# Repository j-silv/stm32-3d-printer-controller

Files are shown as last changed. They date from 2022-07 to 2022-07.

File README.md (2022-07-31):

# STM32 Nucleo 3D printer controller
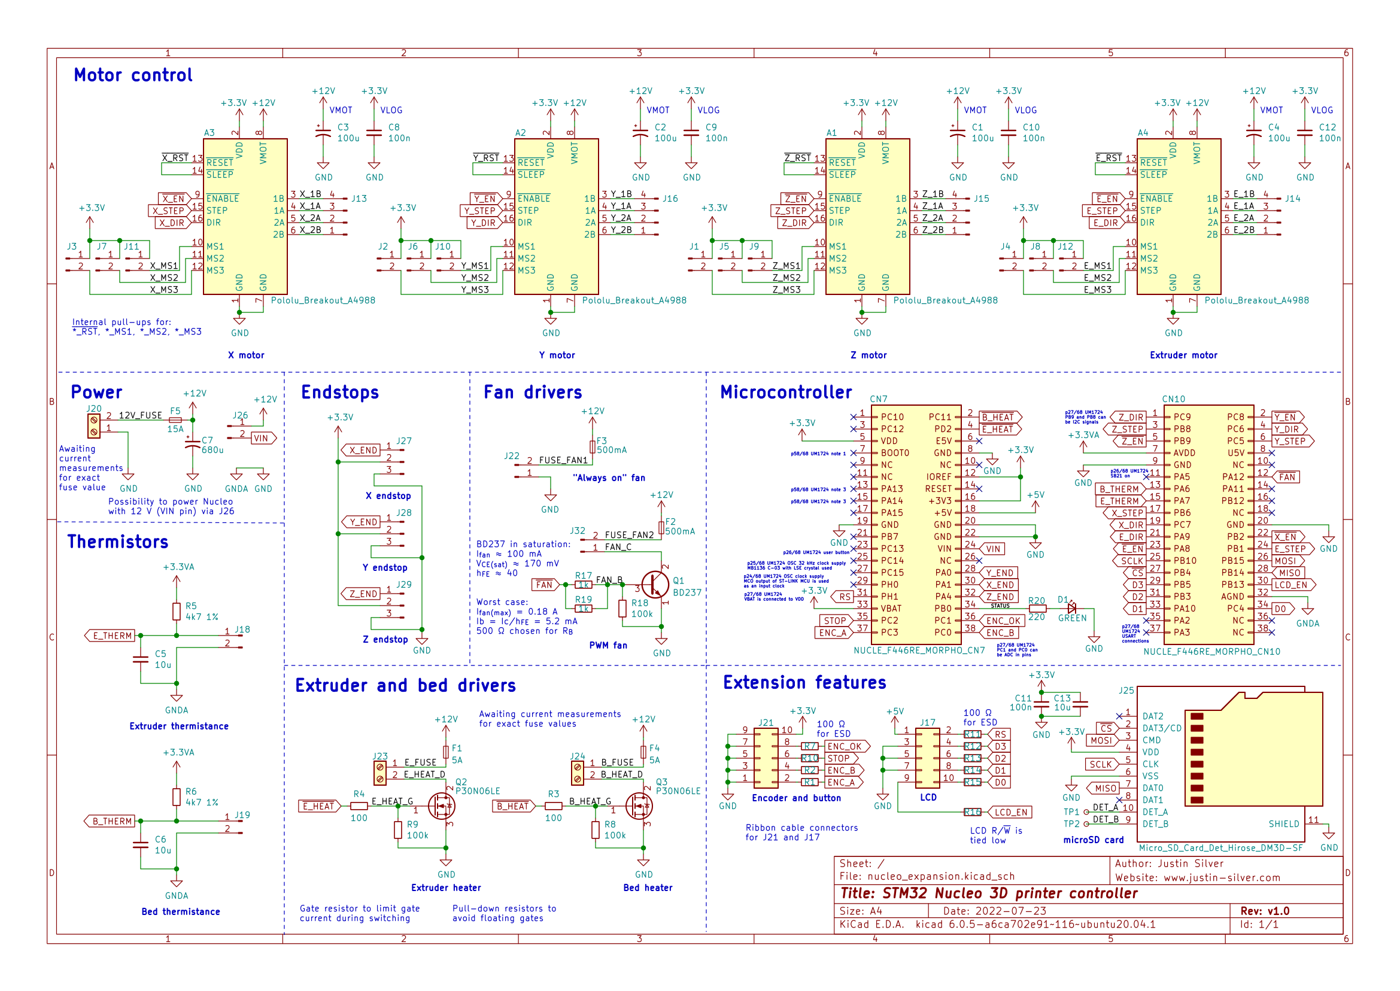
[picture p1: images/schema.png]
Kicad schematic

This project concerns the replacement of a Teensylu 3D printer controller board for a [uDelta RepRap printer](https://reprap.org/wiki/Micro_Delta). An STM32 NUCLEO-F446RE expansion board (shield) is currently being developed as the replacement. After the board is designed and fabricated, the Marlin open source firmware will be configured for use with the Nucleo board.

# Folder structure

**./kicad/stm32_nucleo_expansion/**
- Contains all the CAD files for the shield PCB

# Power usage
I will be using a [S-240-12 12 V 240 W power supply](https://www.meanwellusa.com/upload/pdf/SP-240/SP-240-spec.pdf) Here is an approximate distribution of the power consumption:

## High power usage

### Pololu stepper motors
- [StepStick from RepRap](https://www.reprap-france.com/produit/363-pilote-de-moteur-pas-a-pas-stepstick)
- Max current of 2 A per coil, with overcurrent output protection at 2.1 A
- On-board current limit via potentiometer needs to be checked (TODO)

### Extruder
- 12 V, 3.5 A (40 W) [as specified here](https://www.reprap-france.com/produit/380-cartouche-de-chauffe-12v-40w)

### Bed
- 12 V, 3.5 A (40 W) [as specified here](https://www.reprap-france.com/produit/1234568345-kit-plateau-chauffant-pour-microdelta-originale)

### Extruder fans
- 12 V, 0.18 A (2.16 W) [as specified here](https://www.reprap-france.com/produit/1234568367-ventilateur-turbine-40x10mm-12v)

## Low power usage

### NUCLEO-F446RE
- Supplied with USB 5 V: [300 mA max input current](https://www.st.com/resource/en/user_manual/um1724-stm32-nucleo64-boards-mb1136-stmicroelectronics.pdf#page=20)
- Supplied with external 12 V: [250 mA max input current](https://www.st.com/resource/en/user_manual/um1724-stm32-nucleo64-boards-mb1136-stmicroelectronics.pdf#page=21)
- Measure current consumed by NUCLEO board via JP5 (TODO)

### Pololu stepper motors
- [Approximately 15 mA consumption](https://www.pololu.com/file/0J450/A4988.pdf) at 3.3 V: 50 mW

### microSD card
- [Approximately 150 mA for standard mode (25 MHz) at 3.3 V](https://images-na.ssl-images-amazon.com/images/I/91tTtUMDM3L.pdf): 500 mW

### LCD
- [Typical 1.1 mA consumption](https://www.openhacks.com/uploadsproductos/eone-1602a1.pdf). At 5 V: 5 mW

# PCB
The shield is a 2-layer board fabricated by JLCPCB. It plugs directly into the NUCLEO-F446RE via two 38-pin morpho connectors.
Top and bottom layer view of PCB

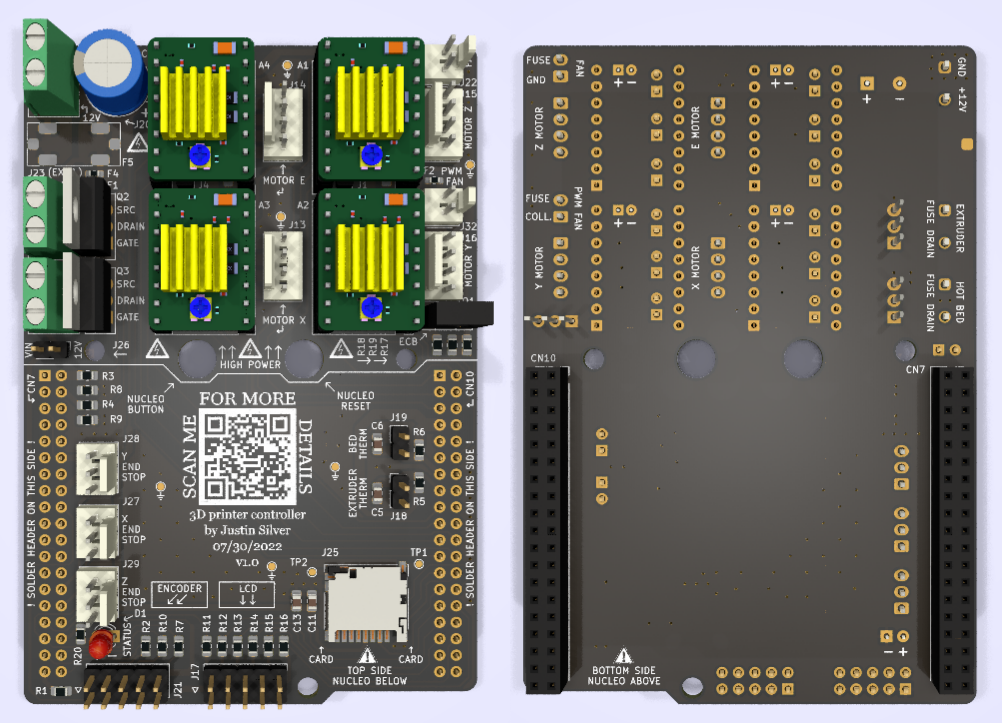
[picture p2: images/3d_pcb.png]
3D view of PCB


# Acknowledgments

- Design inspired by [Teensylu RepRap](https://reprap.org/wiki/Teensylu/fr)
- Kudos to [mobilinkd](https://github.com/mobilinkd/stm-morpho-template) for the STM32 morpho connector template
- Kudos to [bettak](https://grabcad.com/library/reprap-stepstick-stepper-motor-driver-module-1) for the RepRap StepStick 3D model
- Thanks to [r/PrintedCircuitBoard on Reddit](https://www.reddit.com/r/PrintedCircuitBoard/) for the advice and comments

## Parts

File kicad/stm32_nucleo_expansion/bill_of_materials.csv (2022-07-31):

Item | Qty | Reference(s) | Value | DigiKey ID | Product
1 | 4 | A1, A2, A3, A4 | Pololu_Breakout_A4988 |  | STEPPER-DRIVER-STEPSTICKS-A4988
2 | 4 | C1, C2, C3, C4 | 100u | 399-6102-ND | ESK107M025AC3AA
3 | 3 | C5, C6, C13 | 10u | 1276-1096-1-ND | CL21A106KOQNNNE
4 | 1 | C7 | 680u | 732-8638-1-ND | 860010475015
5 | 5 | C8, C9, C10, C11, C12 | 100n | 1276-1003-1-ND | CL21B104KBCNNNC
6 | 1 | CN7 | NUCLE_F446RE_MORPHO_CN7 | S7122-ND | PPPC192LFBN-RC
7 | 1 | CN10 | NUCLE_F446RE_MORPHO_CN10 | S7122-ND | PPPC192LFBN-RC
8 | 1 | D1 | GREEN
9 | 2 | F1, F4 | 5A | 2315-FMC16502WHTPCT-ND | FMC16502WHTP
10 | 2 | F2, F3 | 500mA | 2315-FMC16501WHTPCT-ND | FMC16501WHTP
11 | 1 | F5 | 15A | 36-3586-ND and F11955-ND | 3586 and 0297015.WXT
12 | 15 | J1, J2, J3, J4, J5, J6, J7, J8, J9, J10, J11, J12, J18, J19, J26 | Conn_01x02_Male
13 | 4 | J13, J14, J15, J16 | Conn_01x04_Male | WM19478-ND | 22280040
14 | 2 | J17, J21 | Conn_02x05_Counter_Clockwise
15 | 3 | J20, J23, J24 | Screw_Terminal_01x02 | 732-10955-ND | 691137710002
16 | 2 | J22, J32 | Conn_01x02_Male | WM19485-ND | 22281020
17 | 1 | J25 | Micro_SD_Card_Det_Hirose_DM3D-SF | H126097CT-ND | DM3D-SF(41)
18 | 3 | J27, J28, J29 | Conn_01x03_Male | WM2792-ND | 22280030
19 | 1 | Q1 | BD237 |  | BD237
20 | 2 | Q2, Q3 | P30N06LE |  | P30N06LE
21 | 12 | R1, R2, R3, R4, R7, R10, R11, R12, R13, R14, R15, R16 | 100 | RHM100KCT-ND | ESR10EZPJ101
22 | 2 | R5, R6 | 4k7 1% | A129546CT-ND | CRGH0805F4K7
23 | 3 | R8, R9, R18 | 100k | RHM100KKCT-ND | ESR10EZPJ104
24 | 2 | R17, R19 | 1k | RNCP0805FTD1K00CT-ND | RNCP0805FTD1K00
25 | 1 | R20 | 220
26 | 2 | TP1, TP2 | TestPoint_Small

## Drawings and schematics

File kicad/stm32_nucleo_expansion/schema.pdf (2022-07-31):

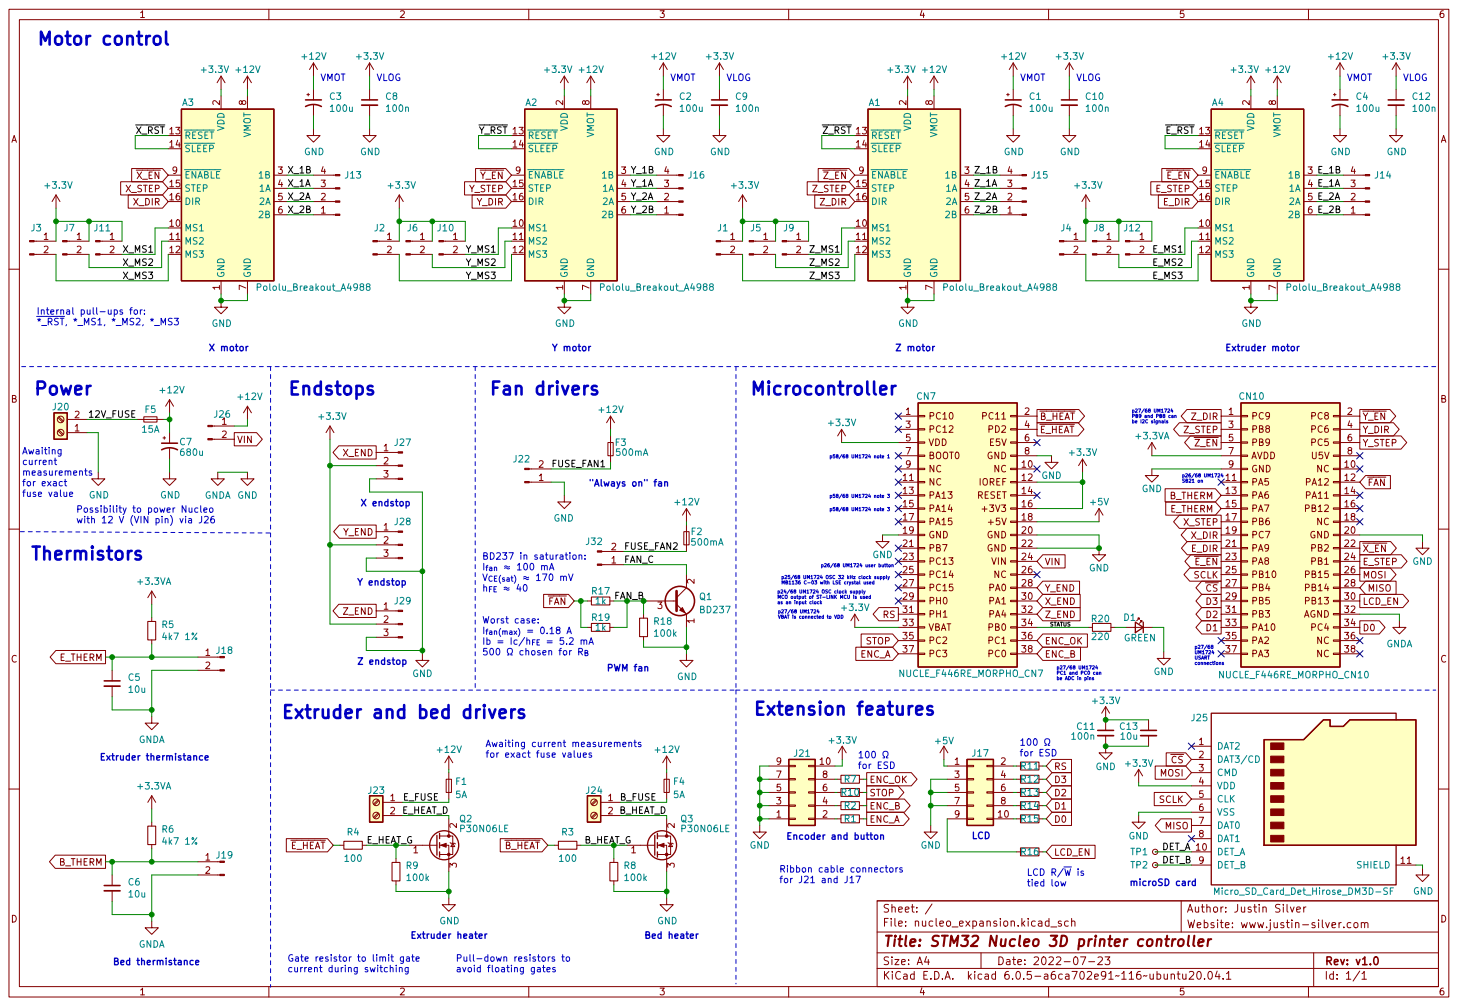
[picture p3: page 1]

p26/68 UM1724 SB21 on Y motor Motor control

1 MS1 10 MS2 11 MS3 12 ~{RESET} 13 ~{SLEEP} 14 STEP 15 DIR 16 VDD

Internal pull-ups for:

Possibility to power Nucleo
with 12 V (VIN pin) via J26
Thermistors

PWM fan BD237 in saturation: þÿI_{fan} "H 100 mA

p25/68 UM1724 OSC 32 kHz clock supply MB1136 C-03 with LSE crystal used

p24/68 UM1724 OSC clock supply MCO output of ST-LINK MCU is used as an input clock p27/68 UM1724 VBAT is connected to VDD

I_{fan(max)} = 0.18 A

be ADC in pins Extruder and bed drivers

for exact fuse values Gate resistor to limit gate

Id: 1/1 Title: STM32 Nucleo 3D printer controller

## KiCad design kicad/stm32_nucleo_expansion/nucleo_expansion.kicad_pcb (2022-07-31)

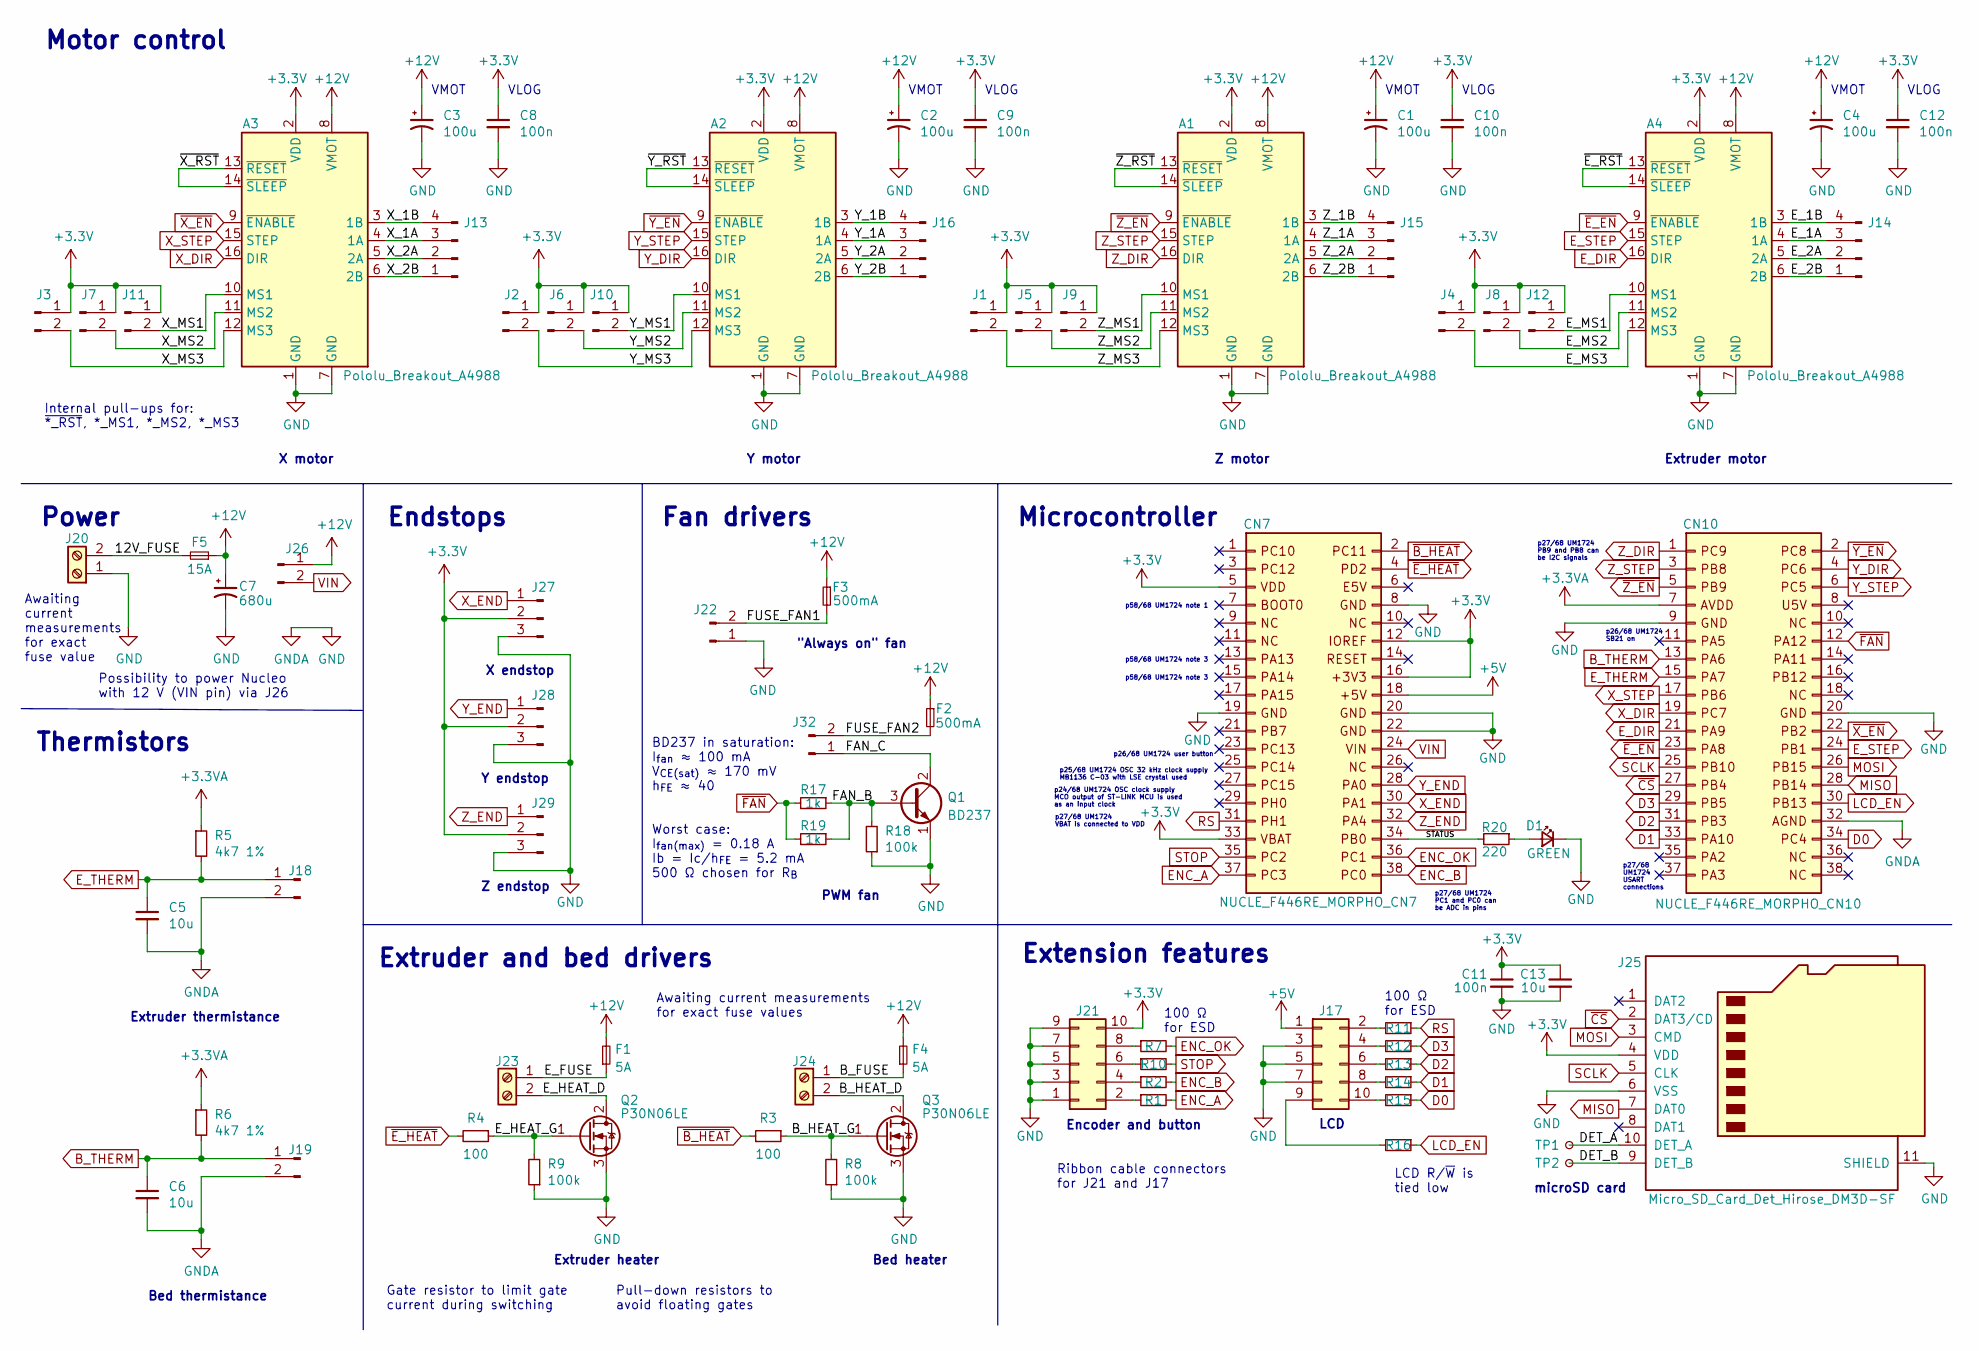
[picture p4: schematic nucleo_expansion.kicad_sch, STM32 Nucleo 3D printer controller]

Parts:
A1, A2, A3, A4: Pololu_Breakout_A4988; Pololu_Breakout-16_15.2x20.3mm
C1, C2, C3, C4: 100u; CP_Radial_D5.0mm_P2.00mm; DigiKey ID 399-6102-ND
C5, C6, C13: 10u; C_0805_2012Metric_Pad1.18x1.45mm_HandSolder; DigiKey ID 1276-1096-1-ND
C7: 680u; CP_Radial_D10.0mm_P5.00mm; DigiKey ID 732-8638-1-ND
C8, C9, C10, C11, C12: 100n; C_0805_2012Metric_Pad1.18x1.45mm_HandSolder; DigiKey ID 1276-1003-1-ND
CN7: NUCLE_F446RE_MORPHO_CN7; PinSocket_2x19_P2.54mm_Vertical; DigiKey ID S7122-ND
CN10: NUCLE_F446RE_MORPHO_CN10; PinSocket_2x19_P2.54mm_Vertical; DigiKey ID S7122-ND
D1: GREEN; LED_D3.0mm
F1, F4: 5A; Fuse_0603_1608Metric_Pad1.05x0.95mm_HandSolder; DigiKey ID 2315-FMC16502WHTPCT-ND
F2, F3: 500mA; Fuse_0603_1608Metric_Pad1.05x0.95mm_HandSolder; DigiKey ID 2315-FMC16501WHTPCT-ND
F5: 15A; 3586_mini; DigiKey ID 36-3586-ND and F11955-ND
J1, J2, J3, J4, J5, J6, J7, J8, J9, J10, J11, J12, J18, J19, J26: Conn_01x02_Male; PinHeader_1x02_P2.54mm_Vertical
J13, J14, J15, J16: Conn_01x04_Male; Molex_KK-254_AE-6410-04A_1x04_P2.54mm_Vertical; DigiKey ID WM19478-ND
J17, J21: Conn_02x05_Counter_Clockwise; PinHeader_2x05_P2.54mm_Vertical
J20, J23, J24: Screw_Terminal_01x02; 691137710002; DigiKey ID 732-10955-ND
J22, J32: Conn_01x02_Male; Molex_KK-254_AE-6410-02A_1x02_P2.54mm_Vertical; DigiKey ID WM19485-ND
J25: Micro_SD_Card_Det_Hirose_DM3D-SF; microSD_HC_Hirose_DM3D-SF; DigiKey ID H126097CT-ND
J27, J28, J29: Conn_01x03_Male; Molex_KK-254_AE-6410-03A_1x03_P2.54mm_Vertical; DigiKey ID WM2792-ND
Q1: BD237; TO-126-3_Vertical
Q2, Q3: P30N06LE; TO-220-3_Vertical
R1, R2, R3, R4, R7, R10, R11, R12, R13, R14, R15, R16: 100; R_0805_2012Metric_Pad1.20x1.40mm_HandSolder; DigiKey ID RHM100KCT-ND
R5, R6: 4k7 1%; R_0805_2012Metric_Pad1.20x1.40mm_HandSolder; DigiKey ID A129546CT-ND
R8, R9, R18: 100k; R_0805_2012Metric_Pad1.20x1.40mm_HandSolder; DigiKey ID RHM100KKCT-ND
R17, R19: 1k; R_0805_2012Metric_Pad1.20x1.40mm_HandSolder; DigiKey ID RNCP0805FTD1K00CT-ND
R20: 220; R_0805_2012Metric_Pad1.20x1.40mm_HandSolder
TP1, TP2: TestPoint_Small; TestPoint_Pad_D1.0mm

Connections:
+3.3VA: CN10.7, R5.1, R6.1
+3V3: A1.2 (VDD), A2.2 (VDD), A3.2 (VDD), A4.2 (VDD), C8.1, C9.1, C10.1, C11.1, C12.1, C13.1, CN7.5, CN7.12, CN7.16, CN7.33, J1.1, J2.1, J3.1, J4.1, J5.1, J6.1, J7.1, J8.1, J9.1, J10.1, J11.1, J12.1, J21.10, J25.4 (VDD), J27.2, J28.2, J29.2
+5V: CN7.18, J17.1
+12V: A1.8 (VMOT), A2.8 (VMOT), A3.8 (VMOT), A4.8 (VMOT), C1.1, C2.1, C3.1, C4.1, C7.1, F1.2, F2.1, F3.1, F4.2, F5.1, J26.1
/12V_FUSE: F5.2, J20.2
/B_FUSE: F4.1, J24.1
/B_HEAT_D: J24.2, Q3.2 (D)
/B_HEAT_G: Q3.1 (G), R3.1, R8.2
/DET_A: J25.10 (DET_A), TP1.1
/DET_B: J25.9 (DET_B), TP2.1
/E_1A: A4.4 (1A), J14.3
/E_1B: A4.3 (1B), J14.4
/E_2A: A4.5 (2A), J14.2
/E_2B: A4.6 (2B), J14.1
/E_FUSE: F1.1, J23.1
/E_HEAT_D: J23.2, Q2.2 (D)
/E_HEAT_G: Q2.1 (G), R4.1, R9.2
/E_MS1: A4.10 (MS1), J12.2
/E_MS2: A4.11 (MS2), J8.2
/E_MS3: A4.12 (MS3), J4.2
/FAN_B: Q1.3 (B), R17.1, R18.2, R19.1
/FAN_C: J32.1, Q1.2 (C)
/FUSE_FAN1: F3.2, J22.2
/FUSE_FAN2: F2.2, J32.2
/STATUS: CN7.34, R20.2
/X_1A: A3.4 (1A), J13.3
/X_1B: A3.3 (1B), J13.4
/X_2A: A3.5 (2A), J13.2
/X_2B: A3.6 (2B), J13.1
/X_MS1: A3.10 (MS1), J11.2
/X_MS2: A3.11 (MS2), J7.2
/X_MS3: A3.12 (MS3), J3.2
/Y_1A: A2.4 (1A), J16.3
/Y_1B: A2.3 (1B), J16.4
/Y_2A: A2.5 (2A), J16.2
/Y_2B: A2.6 (2B), J16.1
/Y_MS1: A2.10 (MS1), J10.2
/Y_MS2: A2.11 (MS2), J6.2
/Y_MS3: A2.12 (MS3), J2.2
/Z_1A: A1.4 (1A), J15.3
/Z_1B: A1.3 (1B), J15.4
/Z_2A: A1.5 (2A), J15.2
/Z_2B: A1.6 (2B), J15.1
/Z_MS1: A1.10 (MS1), J9.2
/Z_MS2: A1.11 (MS2), J5.2
/Z_MS3: A1.12 (MS3), J1.2
/~E_RST: A4.13 (~RESET), A4.14 (~SLEEP)
/~X_RST: A3.13 (~RESET), A3.14 (~SLEEP)
/~Y_RST: A2.13 (~RESET), A2.14 (~SLEEP)
/~Z_RST: A1.13 (~RESET), A1.14 (~SLEEP)
B_THERM: C6.1, CN10.13, J19.1, R6.2
D0: CN10.34, R15.1
D1: CN10.33, R14.1
D2: CN10.31, R13.1
D3: CN10.29, R12.1
ENC_A: CN7.37, R1.2
ENC_B: CN7.38, R2.2
ENC_OK: CN7.36, R7.2
E_DIR: A4.16 (DIR), CN10.21
E_STEP: A4.15 (STEP), CN10.24
E_THERM: C5.1, CN10.15, J18.1, R5.2
GND: A1.1 (GND), A1.7 (GND), A2.1 (GND), A2.7 (GND), A3.1 (GND), A3.7 (GND), A4.1 (GND), A4.7 (GND), C1.2, C2.2, C3.2, C4.2, C5.2, C6.2, C7.2, C8.2, C9.2, C10.2, C11.2, C12.2, C13.2, CN7.8, CN7.19, CN7.20, CN7.22, CN10.9, CN10.20, CN10.32, D1.1 (K), J17.3, J17.5, J17.7, J18.2, J19.2, J20.1, J21.1, J21.3, J21.5, J21.7, J21.9, J22.1, J25.6 (VSS), J25.11 (SHIELD), J27.3, J28.3, J29.3, Q1.1 (E), Q2.3 (S), Q3.3 (S), R8.1, R9.1, R18.1; also elsewhere on the board
LCD_EN: CN10.30, R16.1
MISO: CN10.28, J25.7 (DAT0)
MOSI: CN10.26, J25.3 (CMD)
unnamed: D1.2 (A), R20.1
unnamed: J17.2, R11.2
unnamed: J17.4, R12.2
unnamed: J17.6, R13.2
unnamed: J17.8, R14.2
unnamed: J17.9, R16.2
unnamed: J17.10, R15.2
unnamed: J21.8, R7.1
unnamed: J21.2, R1.1
unnamed: J21.4, R2.1
unnamed: J21.6, R10.1
RS: CN7.31, R11.1
SCLK: CN10.25, J25.5 (CLK)
STOP: CN7.35, R10.2
VIN: CN7.24, J26.2
X_DIR: A3.16 (DIR), CN10.19
X_END: CN7.30, J27.1
X_STEP: A3.15 (STEP), CN10.17
Y_DIR: A2.16 (DIR), CN10.4
Y_END: CN7.28, J28.1
Y_STEP: A2.15 (STEP), CN10.6
Z_DIR: A1.16 (DIR), CN10.1
Z_END: CN7.32, J29.1
Z_STEP: A1.15 (STEP), CN10.3
~B_HEAT: CN7.2, R3.2
~CS: CN10.27, J25.2 (DAT3/CD)
~E_EN: A4.9 (~ENABLE), CN10.23
~E_HEAT: CN7.4, R4.2
~FAN: CN10.12, R17.2, R19.2
~X_EN: A3.9 (~ENABLE), CN10.22
~Y_EN: A2.9 (~ENABLE), CN10.2
~Z_EN: A1.9 (~ENABLE), CN10.5

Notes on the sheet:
100 Ω for ESD
VMOT
Extension features
Pull-down resistors to avoid floating gates
"Always on" fan
VLOG
p27/68 UM1724 PC1 and PC0 can be ADC in pins
Extruder motor
p24/68 UM1724 OSC clock supply MCO output of ST-LINK MCU is used as an input clock
X motor
LCD R/~{W} is tied low
BD237 in saturation: I_{fan} ≈ 100 mA V_{CE(sat)} ≈ 170 mV h_{FE} ≈ 40 Worst case: I_{fan(max)} = 0.18 A Ib = Ic/h_{FE} = 5.2 mA 500 Ω chosen for R_{B}
Awaiting current measurements for exact fuse values
Encoder and button
Possibility to power Nucleo with 12 V (VIN pin) via J26
p27/68 UM1724 USART connections
Thermistors
Y endstop
LCD
Fan drivers
p26/68 UM1724 SB21 on
p27/68 UM1724 VBAT is connected to VDD
Bed heater
Gate resistor to limit gate current during switching
microSD card
Ribbon cable connectors for J21 and J17
p27/68 UM1724 PB9 and PB8 can be I2C signals
PWM fan
Extruder and bed drivers
p58/68 UM1724 note 1
Z endstop
Bed thermistance
Endstops
p58/68 UM1724 note 3
Y motor
Extruder heater
Extruder thermistance
Microcontroller
Motor control
Power

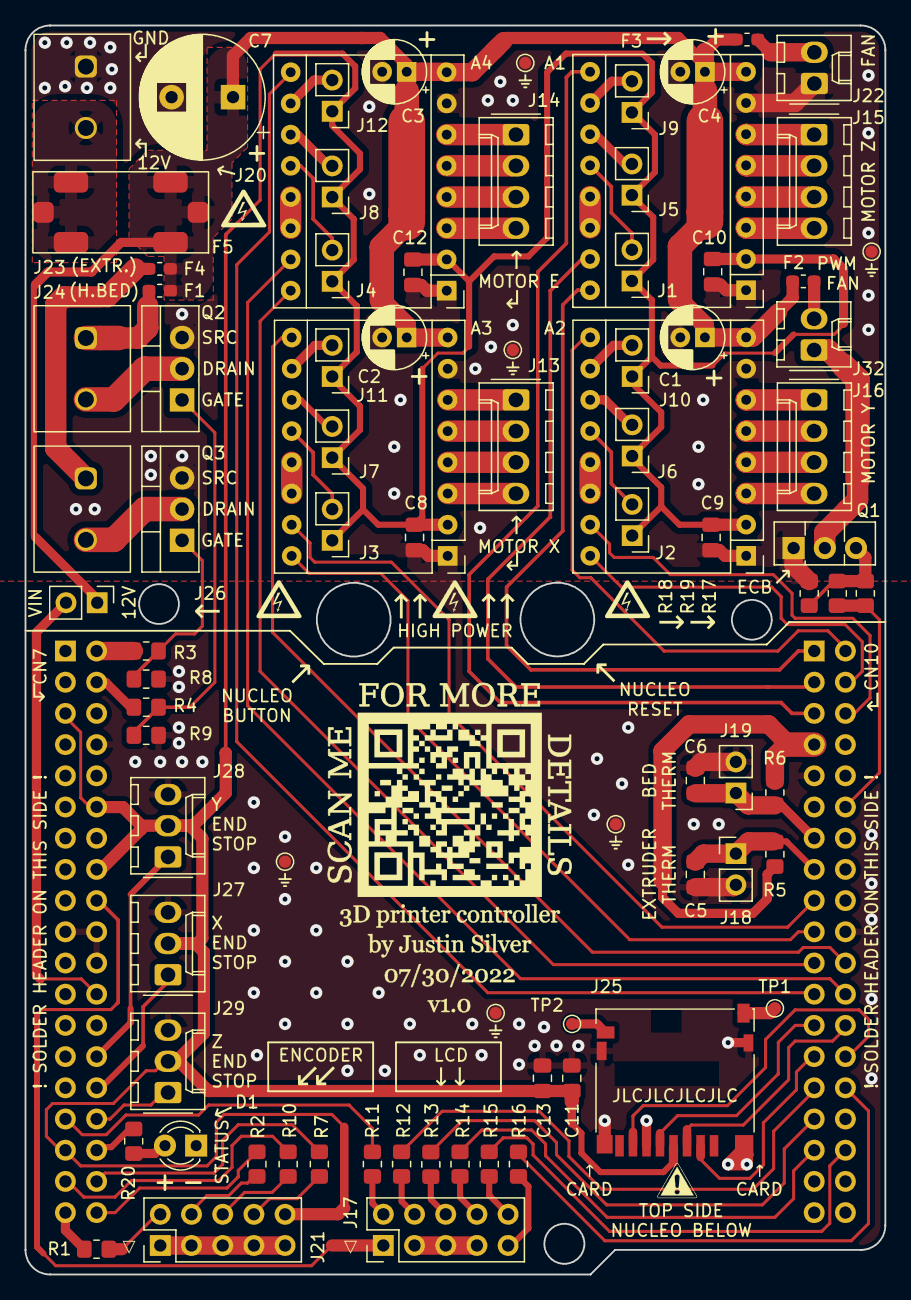
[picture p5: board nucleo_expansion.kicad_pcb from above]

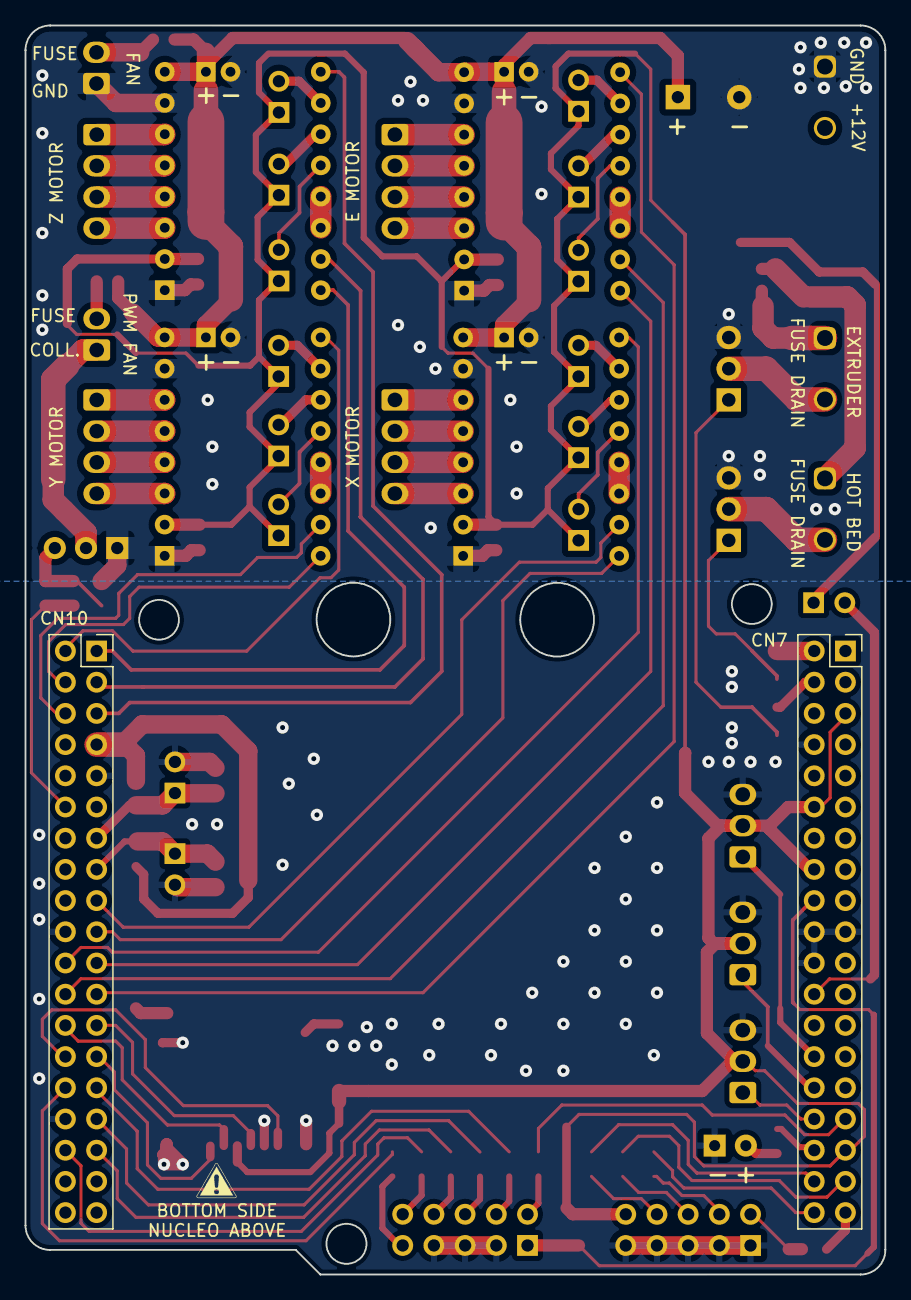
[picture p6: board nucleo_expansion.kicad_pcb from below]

Board: 2 copper layers, 70.0 x 101.7 mm, 86 parts (2 on the bottom side), 97 nets.

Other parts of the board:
⏚: TestPoint_Pad_D1.0mm
⏚#2, ⏚#3, ⏚#4, ⏚#5, ⏚#6: TestPoint_Pad_D1.0mm

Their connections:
GND: ⏚.1, ⏚#2.1, ⏚#3.1, ⏚#4.1, ⏚#5.1, ⏚#6.1; also elsewhere on the board

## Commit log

2022-07-23 Initial commit - add all CAD files
    v1.0 of PCB
    [nucleo_expansion.kicad_pcb, nucleo_expansion.kicad_sch]
2022-07-23 Add schematic pdf and clear ERC markers
    [nucleo_expansion.kicad_sch]
2022-07-23 Add Gerber output files
    [nucleo_expansion-B_Cu.gbr, nucleo_expansion-Edge_Cuts.gbr, nucleo_expansion-F_Cu.gbr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]
2022-07-24 Clean up schematic and PCB
    [nucleo_expansion.kicad_pcb, nucleo_expansion.kicad_sch]
2022-07-24 Update Gerber files
    [nucleo_expansion-B_Cu.gbr, nucleo_expansion-Edge_Cuts.gbr, nucleo_expansion-F_Cu.gbr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]
2022-07-31 Update schematic, PCB, and README (fab send-off v1.0)
    SCHEMATIC:
    - Clean up, rearrange some parts of the schematic
    - Replace one of the "always on" fans with a PWM control using a BJT (BD237)
    - Add fuses for fans
    - Add fuse for main power (SMT fuse blade holder)
    - Add fuse for extruder
    - Add fuse for bed heater
    - Add GPIO series resistors for off-board ribbon connections (ESD)
    - Add microSD card decoupling capacitors
    - Add decoupling capacitor for Pololu logic supply (3.3 V)
    - Choose parts for NMOS drivers (original Teensylu MOSFETs)
    - Choose gate resistors for NMOS (100 ohms)
    - Add green status LED to free STM32 pin
    - Add testpoints for microSD card detect pins
    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
    [bill_of_materials.csv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]
2022-07-31 Add images (schematic, PCB) and .gitignore file

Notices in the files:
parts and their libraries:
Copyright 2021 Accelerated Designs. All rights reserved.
